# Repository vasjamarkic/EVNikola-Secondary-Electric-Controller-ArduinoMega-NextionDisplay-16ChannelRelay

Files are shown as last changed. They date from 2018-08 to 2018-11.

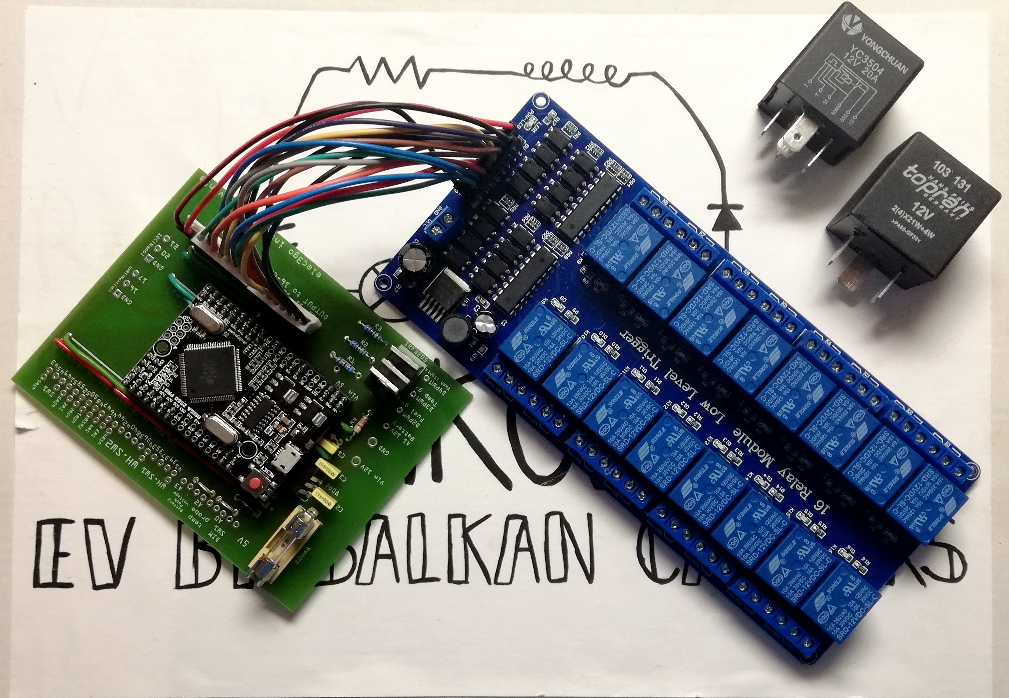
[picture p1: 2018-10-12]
mega2560_sheild and relay module connected.jpg

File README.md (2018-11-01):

# EVNikola-Secondary-Electric-Controller-ArduinoMegaPRO-NextionDisplay-i2cNano-16ChannelRelay
With Arduino Mega Robodyn Mini and Nextion touch display creating controller for lights and other actuators in VW T3.

Still to do:
- 
- recheck the code for wipers
- 
- place the battery and fusses under the co-driver's seat //insulate with plastic or plexi 
- wire the switches and microswitches in Nicola (test again the functions - wipers!!!)
- dismount the top dashboard
- get the front wipers and test it
- install the pwm module for the heating sistem. 
- clean and test the fan - putting the electric heater ??? use a fuse for that ...
- buy a heater (120 V DC) ??? Amazoon for 30 $ ....
- install the remaining front lights
- wire the key ignition switch with f16 and to Emsiso.
- solid the N.C. micro switch for handbrake
- solder the white LED and resistors, make connection types and place it in the dash, via PWM output. 

What was done:
- ordered the PCB board in Svet-elektronike (44 €), aquired.
- mount and assemble the pcb mega sheild (solder holders, mosfet, bridges, resistors, condensators, diodes, tube fuse ...)
- installed the rear LED lights (the small for targa not yet) (90 €)
- bought misc. material in EVJ (240 + 45 €)
- bought 4 relays (35 €), also from ebay for wipers
- wired the back lights and placed terminal under driver seat
- placed wires from fuses compartment (passenger seat) to central circuit compartments (driver seat)
- unmount fuel tank
- bought hexagonal spacers M3 >22 mm lenght (metal or nylon) - done, but will use 16-channel relay module!!! 
- mapping of all wires, matching with entities, dashboard, instrument board, ...
- Put in order de Relays with his functions.
- Choosed the fuses # for actuators 
- updated the drawing VISIO
- emergency stop lights with activating both turning lights - SOLVED with array and switch-case
- replaced the mega2560 with the new one because I accidently bricked 12V to the input pin --> UART is damaged, the procesor is not   
  communicating with pC anymore!
- wired the front-mask! 
- defined the 2d pack of fuses for PWM, Radio, cabin lights, other, Emsiso controller
- wired the wires and second fuse unit (f11 ÷ f16)
- placed wires from second pack fuses (f11 ÷ f16) to dashboard
- blinknig relay working
- placed the circuit box under the driver's seat
- wired the key ignition switch with fuse f10 to MCU.
- placed the wires for all dashboard switches (blue and white thin wires)

by Vasja Markič,
CEO at Elec3go Institute, SI

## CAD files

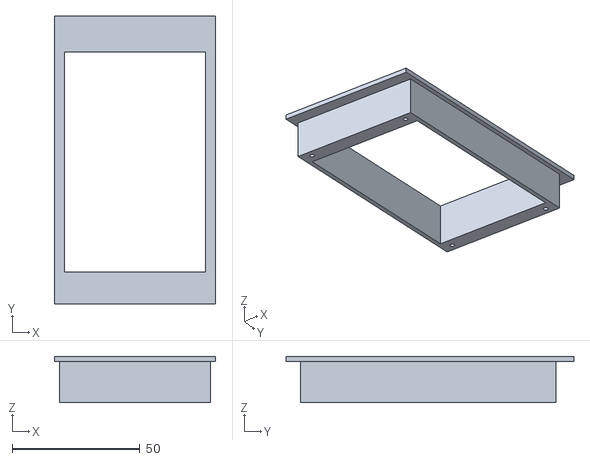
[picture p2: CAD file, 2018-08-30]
nextion2-vlozek.stl
63.0 x 112.5 x 18.0

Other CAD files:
nextion.skp

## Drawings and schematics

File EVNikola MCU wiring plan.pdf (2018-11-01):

# Top view GND

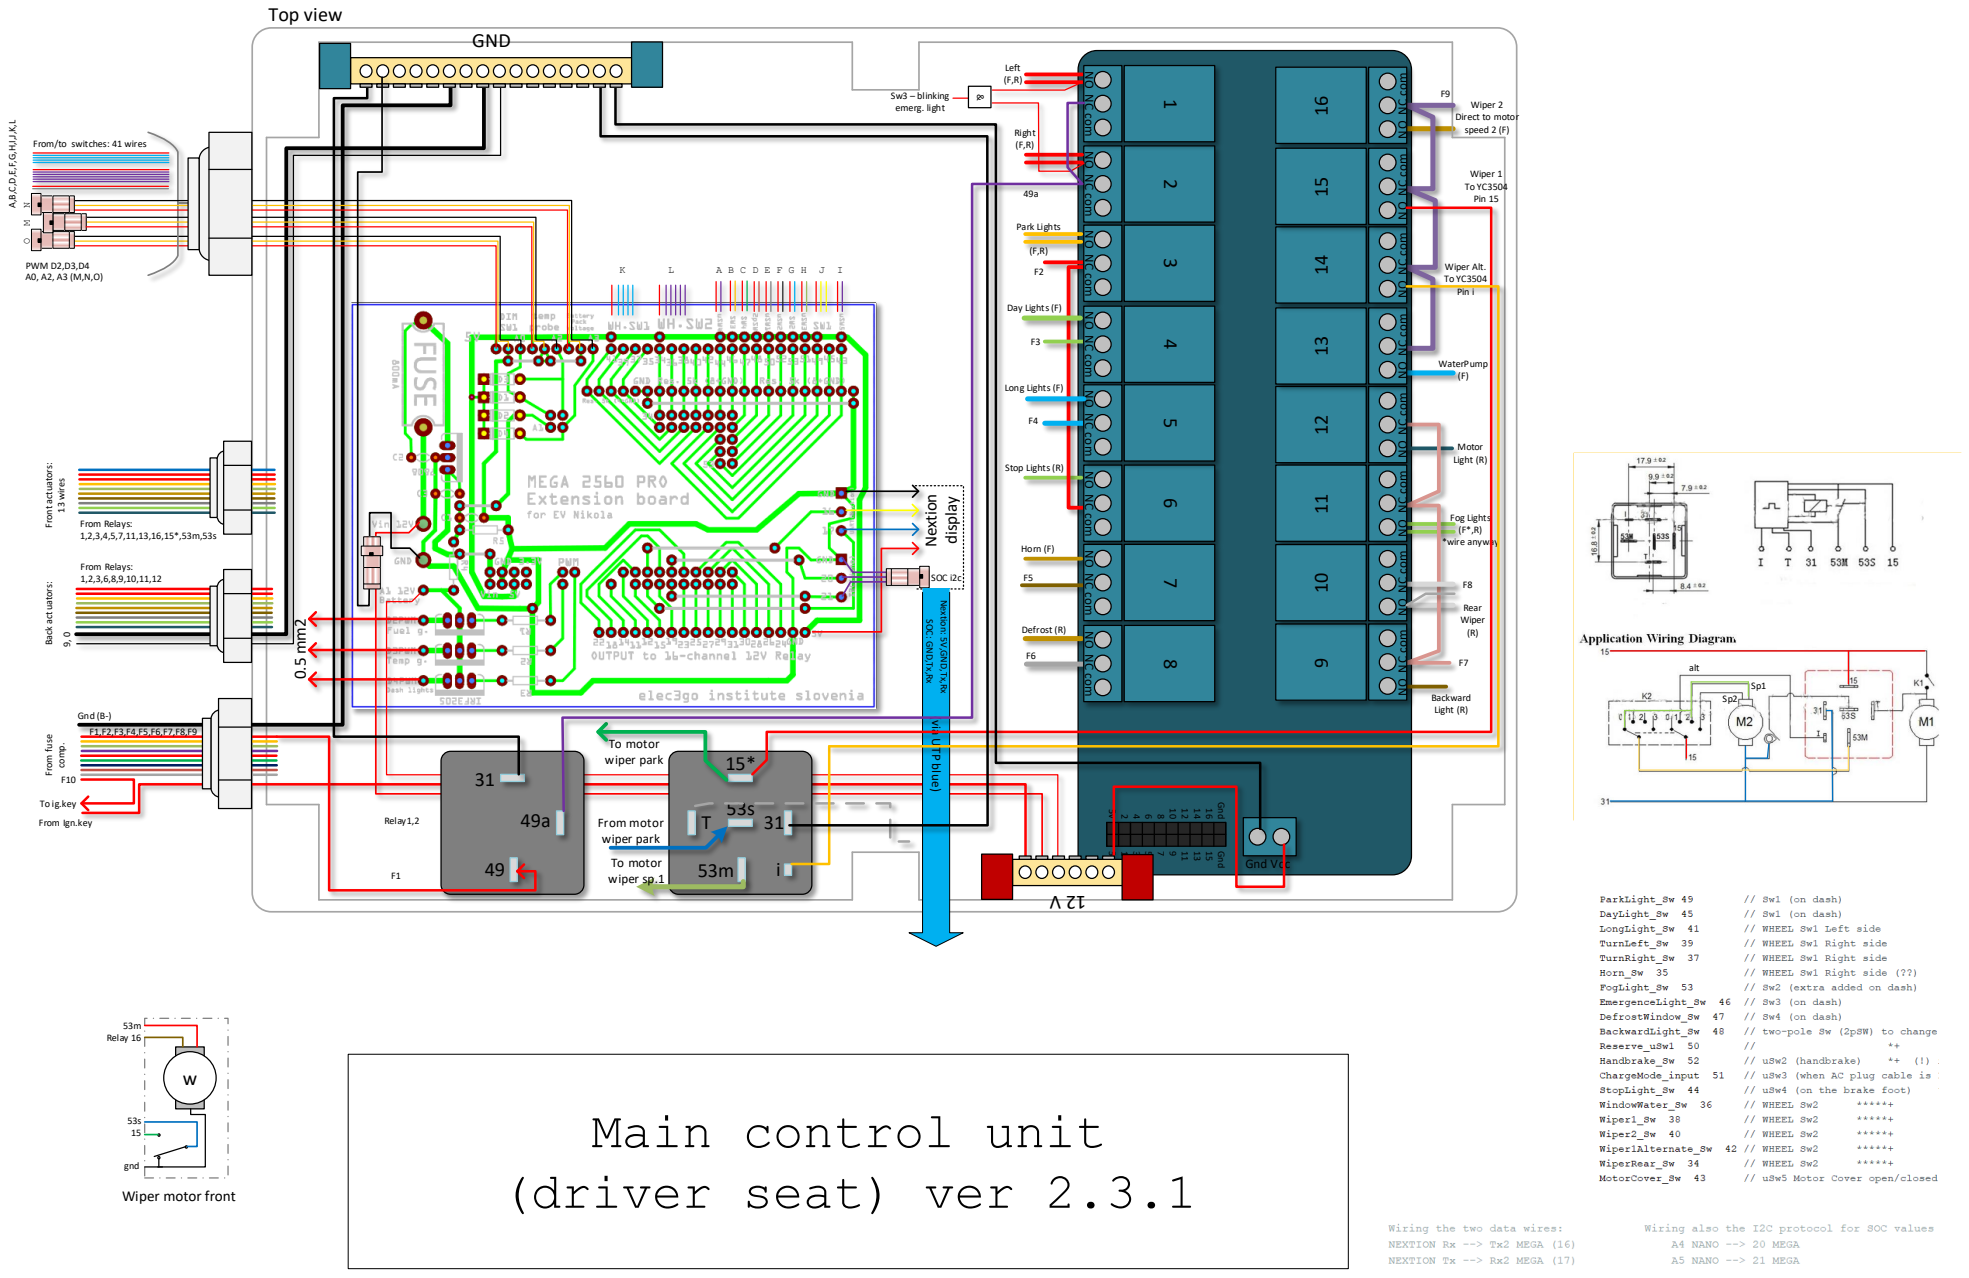
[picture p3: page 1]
Left (F,R); Right (F,R); Park Lights (F,R); Day Lights; Long Lights; Stop Lights; Horn; Defrost; Backward Light; Rear Wiper (R); Fog Lights (F*,R); *wire anyway; Motor Light; WaterPump (F); Wiper; 2 Direct to motor speed 2; alt; – blinking emerg. light; Gnd Vcc; Gnd; From Ign; .key; m Relay 16; Back actuators:; From Relays: 1,2,3,6,8,9,10; Front actuators:; 13 wires; From Relays: 1,2,3,4,5,7,11; PWM D; Nextion; display; SOC i; From; To motor wiper park; From motor wiper park; To motor wiper sp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

NO NC com

/to switches: 41 wires

Nextion: 5V,GND,Tx,Rx

SOC: GND,Tx,Rx

(via UTP blue)

Main control unit
(driver seat) ver

gnd
Wiper motor front

# Rear roof:

3

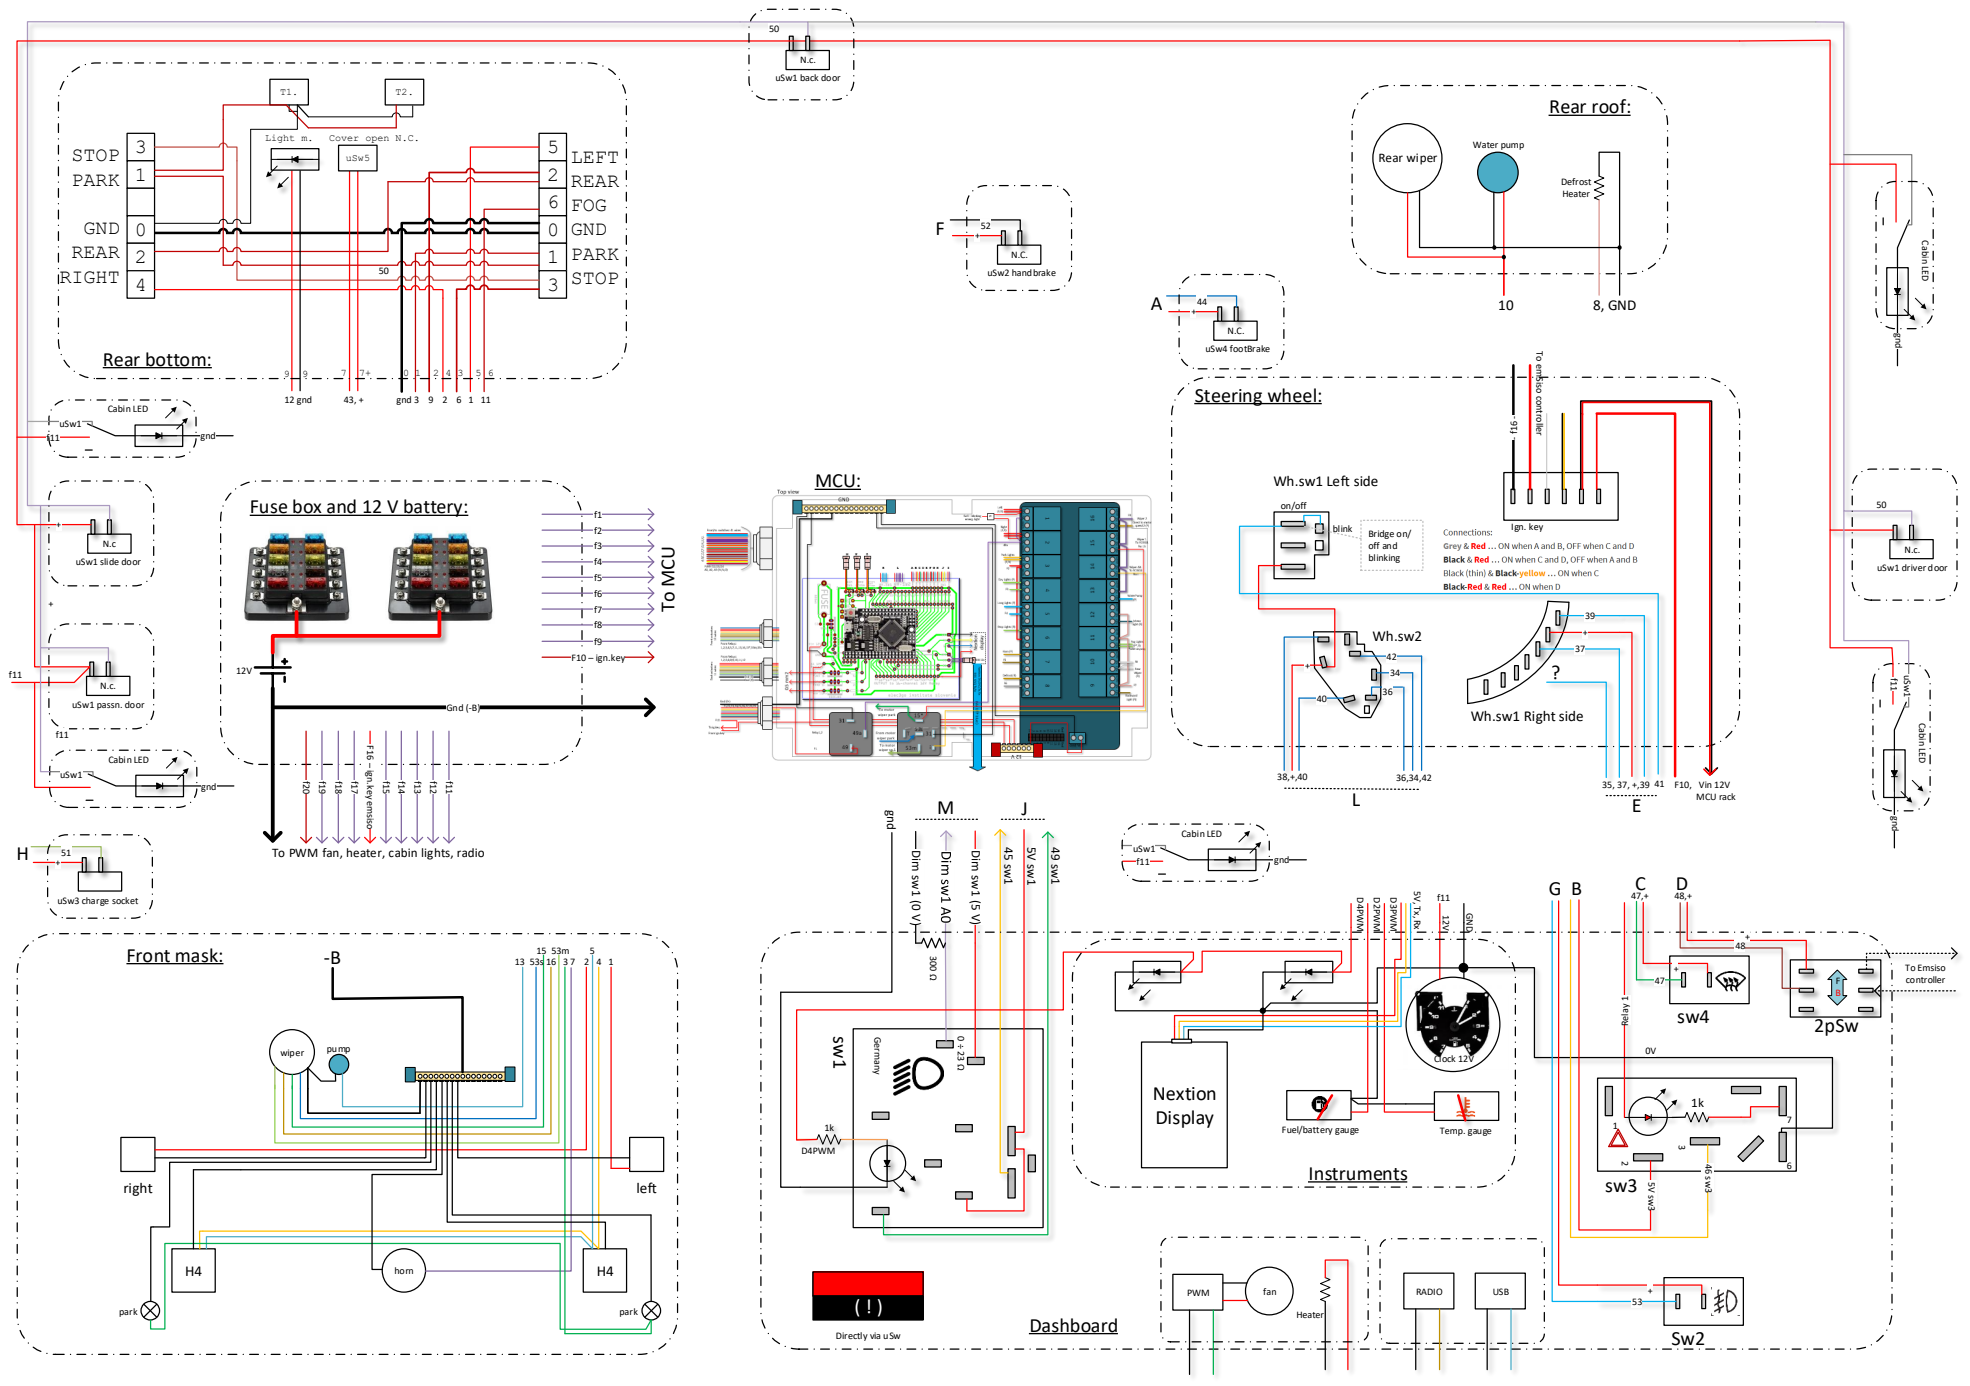
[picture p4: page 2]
Steering wheel:; 2pSw; Ign. key; Germany; Dim sw1 (0 V); Dim sw1 (5 V); D4PWM; To Emsiso controller; uSw1 driver door; uSw1 passn. door; uSw1 slide door; uSw1 back door; uSw2 handbrake; uSw3 charge socket; uSw4 footBrake; STOP; PARK; GND; REAR; RIGHT; LEFT; FOG; Rear bottom:; Cover open N.C.; uSw5; Light m.; 12 gnd; gnd 3 9 2 6 1 11; Front mask:; right; left; horn; park; wiper; pump; Dashboard; Fuel/battery gauge; Temp. gauge; D3PWM; D2PWM; Nextion Display; Instruments; Clock 12V; Relay 1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

To emSiso controller

Wh.sw1 Left side

Fuse box and 12 V battery:

Wh.sw1 Right side

F16 – ign.key emsiso

To PWM fan, heater, cabin lights, radio

Directly via uSw

F1
F2

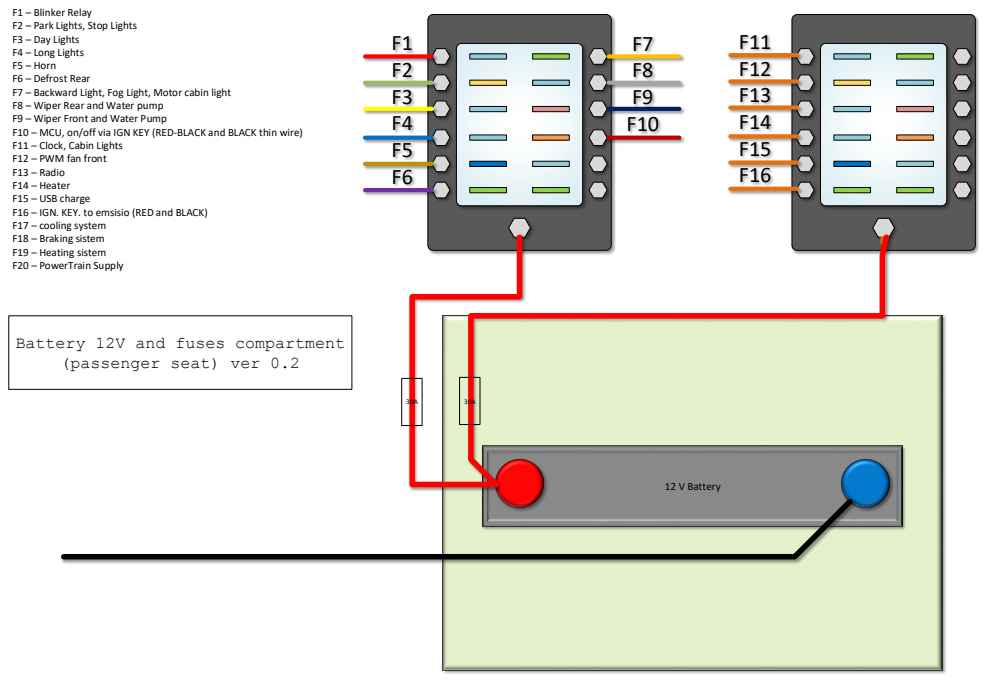
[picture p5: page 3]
12 V Battery

F1 – Blinker Relay
F2 – Park Lights, Stop Lights
F3 – Day Lights
F4 – Long Lights
F5 – Horn
F6 – Defrost Rear
F7 – Backward Light, Fog Light, Motor cabin light
F8 – Wiper Rear and Water pump
F9 – Wiper Front and Water Pump
F10 – MCU, on/off via IGN KEY (RED-BLACK and BLACK thin wire)
F11 – Clock, Cabin Lights
F12 – PWM fan front
F13 – Radio
F14 – Heater
F15 – USB charge
F16 – IGN. KEY. to emsisio (RED and BLACK)
F17 – cooling system
F18 – Braking sistem
F19 – Heating sistem
F20 – PowerTrain Supply

Battery 12V and fuses compartment

(passenger seat) ver 0.2

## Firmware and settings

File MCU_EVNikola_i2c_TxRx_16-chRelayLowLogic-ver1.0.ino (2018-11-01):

/*FIRST version NEXTION display with ARDUINO mega2560 PRO, connection working 
linked with HMI file "NEXTION_Nikola.hmi"
in "nexConf.h" enable debug and must be set to Serial2 ...
Wiring the two data wires:            Wiring also the I2C protocol for SOC values from arduino NANO
NEXTION Rx --> Tx2 MEGA (16)              A4 NANO --> 20 MEGA
NEXTION Tx --> Rx2 MEGA (17)              A5 NANO --> 21 MEGA
The input signals are Swing icons on display - I used ProgressBAR for that trick!
Make sure you import the ITEADlib library in arduino IDE!!
The Relay module has to be connected to power a 10 seconds after the key power the Arduino & Nextion to prevent Swing relays ON!
Dimming the display with tuch function (Nextion code)
Dimming the dash lights with potentimeter on dashboard Sw1
11.9. 2018 fix the code (I/O pins) for MEga PRO CH340G. PINS from 2 ÷ 13 are PWM. 
13.9.2018 Upddated the pin numbers for the Shield (fritzing PCB sheme), emergency lights will turn with both Relay 4 and 5 
via 103 131 topran 12V flashing relay: pins - 49 (+12V), 49a (LOAD), 31 (GND)
Added MotorCover microSw Input and Motor compartment light (Output)
Relay 12 turns the motorlights.
30.9.2018 Updated the Output pins with shematic "EVnikola Omarca Robodyn krmilje postavitev" (VISIO)
24.10. Solved the sloow switching - using an Array for storing input states, then aktivating the logic only when the change is commited, 
Using indexing and switch-case! Also the emergency outputs works fine now!!!
26.10. eliminated all small errata in I/O displaying Nextion, added a graphic shiny LED!

Author: Vasja Markič           
*/
#include <Wire.h>
#include <doxygen.h>
//#include <NexButton.h>
#include <NexConfig.h>
//#include <NexCrop.h> //#include <NexGauge.h> //#include <NexHardware.h> //#include <NexHotspot.h> //#include <NexObject.h> //#include <NexPage.h>
#include <NexPicture.h>
#include <NexProgressBar.h>
//#include <NexSlider.h> //#include <NexText.h>
#include <Nextion.h>
#include <NexTouch.h>
//#include <NexWaveform.h>
#include "Nextion.h"

// OUTPUTS pin declaration:
#define TurnLeft 22              // relay 1 - 2x left turning lights (via flashing relay 103 131)
#define TurnRight 25             // relay 2 - 2x right turning lights (via flashing relay 103 131) (both - emergency stop - turns on via Sw3)
#define ParkLight 18             // relay 3 - 2x front parklights, 2x back parklights + registratiton tables lights, PWM dashboard ON
#define DayLight  27             // relay 4 - 2x front daylights H4
#define LongLight  14            // relay 5 - 2x front longlights H4
#define StopLight  29            // relay 6 - 2x back stoplights
#define Horn  11                 // relay 7 - to horn acuator
#define DefrostWindow  31        // relay 8 - to rear window defrost
#define BackwardLight  12        // relay 9 - to rear backlight(s)
#define WiperRear  30            // relay 10 - motorpump rear AND motor wiper rear
#define FogLight  15             // relay 11 - 2x front foglights
#define MotorLight  28           // relay 12 - lights when cover motor is up ...
#define WindowWater  19          // relay 13 - motorpump front
#define Wiper1Alternate  26      // relay 14 - via auto wiper intermittent relay to motor wiper front, timer
#define Wiper1  23               // relay 15 - wire to auto wiper intermittent relay
#define Wiper2  24               // relay 16 - wire directly to wiper motor
// 21, 20 reserved for I2C comm with NANO soc-meter
// 17, 16 reserved for Tx2 and Rx2 comm with Nextion display
// 13 reserved integrated LED       // n.c.

// PWM OUTUPTS (from 0 ÷ 13)
#define DashLightPWM  4   // dimm dashboard lights
#define TempGaugePWM  3    // drive temp. gauge
#define FuelGaugePWM  2    // drive voltage pack (ex. fuel) gauge

// INPUTS:
#define ParkLight_Sw 49        // Sw1 (on dash)                 **+ --> 3x singal wires, 1x GND and 1x 5V supply
#define DayLight_Sw  45        // Sw1 (on dash)                 **+
#define LongLight_Sw  41       // WHEEL Sw1 Left side           ****+  --> 4x signal wires and 1x 5V supply
#define TurnLeft_Sw  39        // WHEEL Sw1 Right side          ****+
#define TurnRight_Sw  37       // WHEEL Sw1 Right side          ****+
#define Horn_Sw  35            // WHEEL Sw1 Right side (??)     ****+
#define FogLight_Sw  53        // Sw2 (extra added on dash)        *+
#define EmergenceLight_Sw  46  // Sw3 (on dash)                    *+
#define DefrostWindow_Sw  47   // Sw4 (on dash)                    *+
#define BackwardLight_Sw  48   // two-pole Sw (2pSW) to change the drive direction! (on dash, added extra!)   *+
#define Reserve_uSw1  50       //                     *+  
#define Handbrake_Sw  52       // uSw2 (handbrake)    *+  (!) icon on NEXTION
#define ChargeMode_input  51   // uSw3 (when AC plug cable is IN, rezervoir tank)   *+
#define StopLight_Sw  44       // uSw4 (on the brake foot)    *+
#define WindowWater_Sw  36     // WHEEL Sw2      *****+
#define Wiper1_Sw  38          // WHEEL Sw2      *****+
#define Wiper2_Sw  40          // WHEEL Sw2      *****+
#define Wiper1Alternate_Sw  42 // WHEEL Sw2      *****+
#define WiperRear_Sw  34       // WHEEL Sw2      *****+
#define MotorCover_Sw  43      // uSw5 Motor Cover open/closed *+

// analoge INPUTS (from A0 ÷ A15)
#define DIM_input  A0                 // potentiometer on Sw1, for dimming the dash Lights    ***-+
#define Battery12V_input  A1          // analog input, resistor divider 1:15 ratio with capacitor   *-+
#define BatteryPackVolt_input  A3     // analog input, 86V ÷ 125V range via resistor divider R1 = 12K, R2 = 500E --> input range 3.44V ÷ 5V   ???? (GND NOT common!)
#define Temperature_input  A2         // depends on the PTK probe!   ???

// ventilation via PWM power module
// heating via high voltage heater???
// display SOC - using existing fuel gauge (0 ÷ 6 V) reading analog IN and drive with digital PWM and MOSFET BS 170 ali BS 107.
// display temp. motor (0 ÷ 6 V)

// variables will change - HIGH state relay OFF:
int ParkLight_Sw_ON = true;
int DayLight_Sw_ON = true;
int LongLight_Sw_ON = true;
int TurnLeft_Sw_ON = true;
int TurnRight_Sw_ON = true;
int EmergenceLight_Sw_ON = true;
int StopLight_Sw_ON = true;
int Horn_Sw_ON = true;
int DefrostWindow_Sw_ON = true;
int BackwardLight_Sw_ON = true;
int CabinLight_Sw_ON = true;
int Reserve_uSw1_ON = true;
int MotorCover_Sw_ON = true;
int Handbrake_Sw_ON = true;
int WiperRear_Sw_ON = true;
int WindowWater_Button_ON = true;
int Wiper1Alternate_Sw_ON = true;
int Wiper1_Sw_ON = true;
int Wiper2_Sw_ON = true;
int FogLight_Sw_ON = true;
int ChargeMode_ON = true;       // if we plug the AC charging
long DIM_Value = 0;      // initial value of the dimming display, from 0 to 1023  (measures 0 ÷ 5 V)
long DIM;                        // DIM transformed to int from 0 ... 100
unsigned int Battery12V_Value = 0;    // initial value od digital value of the 12 V battery (0 ÷ 1023) 
unsigned int BatteryPackVolt_Value = 0;
unsigned int Temperature_Value = 0;
unsigned int Battery12V_treshold = 11;   // set the min. voltage for signaling battery low voltage on display
float Battery12V;
long BatteryPackVolt;      // transform 3.44V to 0 and 5.00V to 40
long Temperature;         // transform 0.00V to 0 and 5.00V to 40
char object[10];
int SOC2;         //aquire from arduino NANO SOC Meter
volatile double ARRAY[20];          // for storing input from switches
volatile double ARRAY_OLD[20];      // the loop before, for trigering an event!

// Declaration of objects in NEXTION
// NexProgressBar - progress bar --> value 100 (is pic1) or 0 (pic0)
// NexButton ...
NexProgressBar j0 = NexProgressBar(0, 3, "j0");   // day lights
NexProgressBar j1 = NexProgressBar(0, 4, "j1");   // long lights
NexProgressBar j2 = NexProgressBar(0, 5, "j2");   //  fog
NexProgressBar j3 = NexProgressBar(0, 6, "j3");   //  left
NexProgressBar j4 = NexProgressBar(0, 7, "j4");   //  right
NexProgressBar j5 = NexProgressBar(0, 8, "j5");   //  EmergenceLight
NexProgressBar j6 = NexProgressBar(0, 9, "j6");   //  handbrake
NexProgressBar j7 = NexProgressBar(0, 10, "j7");   //  batery low
NexProgressBar j8 = NexProgressBar(0, 11, "j8");   //  defrozing window
NexProgressBar j9 = NexProgressBar(0, 12, "j9");      // AC recharge lightning
NexProgressBar j10 = NexProgressBar(0, 13, "j10");    // "Nicola" text diplay or "Charging" text display
NexProgressBar j11 = NexProgressBar(0, 14, "j11");    // Displaying the progress bar value of SOC, "0" empty, "100" full.
// write here for displaying SOC value ...
NexProgressBar j12 = NexProgressBar(0, 15, "j12");    // icon charging inside the van
NexProgressBar j13 = NexProgressBar(0, 16, "j13");    // slider of Dimming brightness of dashboard lights
NexProgressBar j14 = NexProgressBar(0, 19, "j14");    // Cover motor open!
NexProgressBar j15 = NexProgressBar(0, 17, "j15");    // Backward icon on display
NexProgressBar j16 = NexProgressBar(0, 20, "j16");    // PARK light

// Declaration of touch events: (temp. the list is empty)
NexTouch *nex_listen_list[] =
{
  NULL
};

//Touch events:
// if needed write down here 

//*******************************************************************************************************
// setup program/sequence:
void setup() {
  nexInit();               // Nextion initalization
  Wire.begin(8);   // I2C !!
  Wire.onReceive(receiveEvent);
  Serial.begin(9600);      // speed of comunication with Arduino

//register the event callback functions of each event
// OUTPUTS:
  pinMode(TurnLeft, OUTPUT);           // relay 1
  pinMode(TurnRight, OUTPUT);          // relay 2
  pinMode(ParkLight, OUTPUT);          // relay 3
  pinMode(DayLight, OUTPUT);           // relay 4
  pinMode(LongLight, OUTPUT);          // relay 5
  pinMode(StopLight, OUTPUT);          // relay 6
  pinMode(Horn, OUTPUT);               // relay 7: 1 x Horn
  pinMode(DefrostWindow, OUTPUT);      // relay 8
  pinMode(BackwardLight, OUTPUT);      // relay 9
  pinMode(WiperRear, OUTPUT);          // relay 10: back wiper and watering
  pinMode(FogLight, OUTPUT);            // relay 11
  pinMode(MotorLight, OUTPUT);          // relay 12 Lights in motor compartment
  pinMode(WindowWater, OUTPUT);         // relay 13 motor of water pump front
  pinMode(Wiper1Alternate, OUTPUT);     // relay 14
  pinMode(Wiper1, OUTPUT);              // relay 15
  pinMode(Wiper2, OUTPUT);              // relay 16 
  pinMode(DashLightPWM, OUTPUT);        // to MOSFET 1  drives dash lights via RELAY 1 (5 V), mosfet driven with 12 V
  pinMode(TempGaugePWM, OUTPUT);        // to MOSFET 2  drives tempertature GAUGE (6 V), mosfet driven on 12 V
  pinMode(FuelGaugePWM, OUTPUT);        // to MOSFET 3 drives fuel GAUGE (6 V), mosfet driven on 12 V
  
// INPUTS:
  pinMode(ParkLight_Sw, INPUT);
  pinMode(DayLight_Sw, INPUT);
  pinMode(LongLight_Sw, INPUT);       
  pinMode(TurnLeft_Sw, INPUT);   
  pinMode(TurnRight_Sw, INPUT);  
  pinMode(StopLight_Sw, INPUT);    // foot pedal microbutton
  pinMode(Horn_Sw, INPUT);         // steering wheel button
  pinMode(DefrostWindow_Sw, INPUT); 
  pinMode(BackwardLight_Sw, INPUT);     // Two-poles Sw 
  pinMode(WiperRear_Sw, INPUT);  
  pinMode(EmergenceLight_Sw, INPUT);   
  pinMode(Reserve_uSw1, INPUT); 
  pinMode(MotorCover_Sw, INPUT);
  pinMode(Handbrake_Sw, INPUT);
  pinMode(FogLight_Sw, INPUT);
  pinMode(WindowWater_Sw, INPUT);       
  pinMode(Wiper1Alternate_Sw, INPUT);  
  pinMode(Wiper1_Sw, INPUT);  // speed 1
  pinMode(Wiper2_Sw, INPUT);  // speed 2 
  pinMode(ChargeMode_input, INPUT); // if the AC cable is pludged
  pinMode(Battery12V_input, INPUT); // ANALOG measurment of voltage 0 ÷ 12 V - wire a voltage divider with resistors 81.3k + (8.25k || 100nF)
  pinMode(DIM_input, INPUT);    // dimming with trimmer on Sw1 (lights), 0 - 5V (1023), could also trim the LCD brightness (ANALOG)
  pinMode(BatteryPackVolt_input, INPUT);   // range from 3.44V (703) to 5V (1023)   (ANALOG)  // GNDs must be separated!!!
  pinMode(Temperature_input, INPUT);    // from 0V (0) to 5V (1023) via PTK   (ANALOG)
  
  relayOFF();       //sets all relay to OFF!
  testDisplay();     // test all the icons for 0.5 sec
}
//***************************************************************************************************
//main loop/program :
void loop() {  
  readDigital();      // reading the input states into an ARRAY
  readAnalog();       // reading the input ANALOG 
  equations();
  writeDigital();    //Solved with software interrupt - if change in switches! Used Switch-Case
  writeAnalog();    
  nexLoop(nex_listen_list);    // reading the touch events on NEXTION display (curently not used)
}
//*********************************************************************************************
//function for reading digital and analog signals in Arduino:
void readDigital() {

// read the state of the inputs and store it in a Array size 20

  for (int i = 0; i < 20; i++) {
  ARRAY_OLD[i]=ARRAY[i];        // store the last data to the ARRAY_OLD.
  }
  ARRAY[0] = digitalRead(TurnLeft_Sw);     //New readings and storing in ARRAY
  ARRAY[1] = digitalRead(TurnRight_Sw);
  ARRAY[2] = digitalRead(ParkLight_Sw);
  ARRAY[3] = digitalRead(DayLight_Sw);
  ARRAY[4] = digitalRead(LongLight_Sw);
  ARRAY[5] = digitalRead(StopLight_Sw);
  ARRAY[6] = digitalRead(EmergenceLight_Sw); 
  ARRAY[7] = digitalRead(ChargeMode_input);
  ARRAY[8] = digitalRead(Horn_Sw);
  ARRAY[9] = digitalRead(DefrostWindow_Sw);
  ARRAY[10] = digitalRead(BackwardLight_Sw);
  ARRAY[11] = digitalRead(WiperRear_Sw);
  ARRAY[12] = digitalRead(Reserve_uSw1);
  ARRAY[13] = digitalRead(MotorCover_Sw);
  ARRAY[14] = digitalRead(Handbrake_Sw);
  ARRAY[15] = digitalRead(FogLight_Sw);
  ARRAY[16] = digitalRead(WindowWater_Sw);
  ARRAY[17] = digitalRead(Wiper1Alternate_Sw);
  ARRAY[18] = digitalRead(Wiper1_Sw);
  ARRAY[19] = digitalRead(Wiper2_Sw);
}
 
//******************************************************************************************
void writeDigital() {
  if (ARRAY != ARRAY_OLD) {              // if any switch activated, one of the digit is different, compare the OLD and NEW ARRAY
    for (int i = 0; i < 20; i++) {       // check all inputs in the array
    if (ARRAY_OLD[i]!=ARRAY[i]){          // when found the index (changed input), change the status!
      switch (i) {
        case 0:                         // turn left
        j3.setValue(ARRAY[i]*100);
        digitalWrite(TurnLeft, !ARRAY[i]);
        break;
        case 1:                       // turn right
        j4.setValue(ARRAY[i]*100);
        digitalWrite(TurnRight, !ARRAY[i]);
        break;
        case 2:                           // park light
        digitalWrite(ParkLight, !ARRAY[i]);
        j16.setValue(ARRAY[i]*100);
        // set PWM D4 LED cockpit ON DIM Value in the function writeAnalog()
        //analogWrite(DashLightPWM,!ARRAY[i]*DIM); --> into the writeAnalog() function
        break;
        case 3:                         // day lights
        j0.setValue(ARRAY[i]*100);
        digitalWrite(DayLight, !ARRAY[i]);
        break;
        case 4:                         // long lights
        j1.setValue(ARRAY[i]*100);
        digitalWrite(LongLight, !ARRAY[i]);
        break;
        case 5:                         // stop light
        digitalWrite(StopLight, !ARRAY[i]);
        break;
        case 6:                         // Emergence blinkers
        digitalWrite(TurnRight, !ARRAY[i]);
        digitalWrite(TurnLeft, !ARRAY[i]);
        j5.setValue(ARRAY[i]*100);
        break;
        case 7:                          // CHARGE mode input
        j9.setValue(ARRAY[i]*100);   //Strela
        j10.setValue(!ARRAY[i]*100);   // Show "charging" 
        j12.setValue(ARRAY[i]*100);    // icon charging
        break;
        case 8:                       // HORN
        digitalWrite(Horn, !ARRAY[i]);
        break;
        case 9:                        // DEFROST
        j8.setValue(ARRAY[i]*100);
        digitalWrite(DefrostWindow, !ARRAY[i]);
        break;
        case 10:                   // BackWard Light
        j15.setValue(ARRAY[i]*100);         // icon going back!!!
        digitalWrite(BackwardLight, !ARRAY[i]);
        break;
        case 11:                          // Wiper REAR + WATER
        digitalWrite(WiperRear, !ARRAY[i]);
        break;
        case 12:                          // RESERVE uSw1
        break;
        case 13:                          // Motor cover - light back motor compartment
        j14.setValue(ARRAY[i]*100);
        digitalWrite(MotorLight, !ARRAY[i]);
        break;
        case 14:                        // Handbrake
        j6.setValue(ARRAY[i]*100);
        break;
        case 15:                        // Fog Light
        j2.setValue(ARRAY[i]*100);
        digitalWrite(FogLight, !ARRAY[i]);
        break;
        case 16:                        // Window WATER front
        digitalWrite(WindowWater, !ARRAY[i]);
        break;
        case 17:                        // Wiper 1 ALT
        digitalWrite(Wiper1Alternate, !ARRAY[i]);
        break;
        case 18:                        // WIPER 1
        digitalWrite(Wiper1, !ARRAY[i]);
        break;
        case 19:                        // WIPER 2
        digitalWrite(Wiper2, !ARRAY[i]);
        break;       
        }
      }
    }
  }
// dim the display - reading DIM_value, using potenciometer on A0
// On nextion HMI file the page0 postinitialize event has code: j13.value=dim
  j13.setValue(DIM);    //displaying the brigtness of the dash lights. 
// Displaying SOC graphic via wire.h on NANO 
  j11.setValue(SOC2);    // when aquiring data from Arduino NANO, change to SOC2! 
//  Serial.println(SOC2);         // for diagnostic!

/* display of low 12v battery icon, if voltage is lower than 11 V reading from A11
  0 - ~17 V voltmeter
  works with 3.3volt and 5volt Arduinos
  uses the stable internal 1.1volt reference
  10k resistor from A0 to ground, and 150k resistor from A0 to +batt
  (1k8:27k or 2k2:33k are also valid 1:15 ratios)
  100n capacitor from A0 to ground for stable readings    */
  Battery12V=Battery12V_Value/19.5533;  // calculation to voltage value
  //Serial.println(Battery12V_Value);   // for monitoring purpouses
  //Serial.println(Battery12V);
  if (Battery12V < Battery12V_treshold) {      //set the voltage treshold
    j7.setValue(100);
    }
  else {
    j7.setValue(0);
    }
}

void writeAnalog() {
  analogWrite(FuelGaugePWM, BatteryPackVolt);   // wire to gauge fuel
  analogWrite(TempGaugePWM, Temperature);       // wire to Temp. gauge. 
  analogWrite(DashLightPWM, ARRAY[2]*DIM);      //the third field in the array is ParkLight input switch.
  }
  
void readAnalog() {
  DIM_Value = analogRead(DIM_input); // reading values from 0 - 5 V and converts to int value from 0 to 1023 .
  Battery12V_Value = analogRead(Battery12V_input);
  BatteryPackVolt_Value = analogRead(BatteryPackVolt_input);
  Temperature_Value = analogRead(Temperature_input);
  }

void equations() {
  //equations for DIMMING LED cockpit lights:
  // 950 --> 100, 1023 --> 255; ???? resistor divider - 300 Ohm and 23 Ohm pot. , 5V --> Max 5 V (1023), Min 4.64 V (950)
  DIM=3.49*(1023-DIM_Value);   //min 0 max 73 --> multiply faktor 3.49 --> min 0 max 255
  //equations for Fuel gauge:
  // 703 --> 0, 1023 --> 255    BUT - GND of the pack is insulated from the circuits!!!
  BatteryPackVolt = (BatteryPackVolt_Value-703)*255/(1023-703);
  //equations for Temperature gauge:
  // 0 --> 0, 1023 --> 255
  Temperature = Temperature_Value*255/1023;
  // sending PWM singal temperature gauge and fuel gauge:
}

//function for reading via I2C the SOC from Nano
void receiveEvent(int howMany) {
  while (1 < Wire.available()) { // loop through all but the last
    char c = Wire.read(); // receive byte as a character
    //Serial.print(c);         // print the character
  }
  SOC2 = Wire.read();    // receive byte as an integer
  //Serial.println(SOC2);         // print the integer
}

// set all relay OFF - for begin sequence!
void relayOFF() {
  digitalWrite(TurnLeft, HIGH);
  digitalWrite(TurnRight, HIGH);
  digitalWrite(ParkLight, HIGH);
  digitalWrite(DayLight, HIGH);
  digitalWrite(LongLight, HIGH);
  digitalWrite(StopLight, HIGH);
  digitalWrite(Horn, HIGH);
  digitalWrite(DefrostWindow, HIGH);
  digitalWrite(BackwardLight, HIGH);
  digitalWrite(WiperRear, HIGH);
  digitalWrite(FogLight, HIGH);
  digitalWrite(MotorLight, HIGH);
  digitalWrite(WindowWater, HIGH);
  digitalWrite(Wiper1Alternate, HIGH);
  digitalWrite(Wiper1, HIGH);
  digitalWrite(Wiper2, HIGH);
  }

void testDisplay() {
  j0.setValue(100);
  j1.setValue(100);
  j2.setValue(100);
  j3.setValue(100);
  j4.setValue(100);
  j5.setValue(100);
  j6.setValue(100);
  j7.setValue(100);
  j8.setValue(100);
  j9.setValue(100);
  j10.setValue(0); 
  j11.setValue(100);
  j12.setValue(100);
  j13.setValue(100);
  j14.setValue(100);
  j15.setValue(100);
  j16.setValue(100);
  delay(500);
   j0.setValue(0);
  j1.setValue(0);
  j2.setValue(0);
  j3.setValue(0);
  j4.setValue(0);
  j5.setValue(0);
  j6.setValue(0);
  j7.setValue(0);
  j8.setValue(0);
  j9.setValue(0);
  j10.setValue(100); 
  j11.setValue(0);
  j12.setValue(0);
  j13.setValue(0);
  j14.setValue(0);
  j15.setValue(0);
  j16.setValue(0);
  }

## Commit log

2018-08-18 Code for Arduino Mega
    Using Arduino Mega in connection with Nextion display, 16-chanell low logic optocoupler relay module.
2018-08-18 Tutorial Nextion
    How to - use, program and connect to Arduino (Mega).
2018-08-29 icons and logo for Nextion display 2.4"
    Black background, icons and battery SOC meter, BalkanCampers logo.
2018-08-30 Holder for Nextion Display
    3D model (sketchup and STL) for Nextion holder for VW T3 instrumentation
    [nextion.skp, nextion2-vlozek.stl]
2018-09-11 Fix the code for the control unit usingROBOTDYN MEGA PRO CH340G /Atmega2560
    Added:
    - 3 PWM outputs for driving the dashboard lights, voltage and temperature gauges
    - 3 analog inputs for measuring dim, voltage of the battery pack (via resistor divider) and temperature.
    Changed:
    - cabin lights will be drived directly! (not via central unit)
    - added the rear wiper function
2018-09-11 PIN chart for Arduino MegaPro
2018-09-13 Version 1.1
    Changed the pin order, according with the PCB sheild drawn in fritzing for MegaPro unit
2018-09-13 Ver 0.1
    Added the holders for MegaPro, resistors, connectors digital I/O, UART and I2C.
    To add security circuit (DIODES), PWM with transistors, analog inputs with dividers and filters, power stabilizer 5 V.
    [ControlUnit Sheild for MegaPro RoboDyn EVNikolaProject PCB.fzz]
2018-09-13 MOSFET irf3205 datasheet
2018-09-13 Updated fritzing and c code for Arduino
    Ver. 1.2
    [ControlUnit Sheild for MegaPro RoboDyn EVNikolaProject PCB.fzz]
2018-09-16 Upper limit for PWM set to 255!
2018-09-17 Added 7805 voltage stabilizator and fuse.
    [ControlUnit Sheild for MegaPro RoboDyn EVNikolaProject PCB.fzz]
2018-09-17 Last version PCB
    [ControlUnit Sheild for MegaPro RoboDyn EVNikolaProject PCB.fzz]
2018-09-19 Added pin 5V to 16-chanel relay output
    [ControlUnit Sheild for MegaPro RoboDyn EVNikolaProject PCB.fzz]
2018-09-30 Updated pins
    Next step: Timer as interupt for blinking
2018-09-30 Wiring diagram for control unit
    The magic box will be placed under the drive's seat.
2018-10-12 last version
    [ControlUnit Sheild for MegaPro RoboDyn EVNikolaProject PCB.fzz]
2018-10-12 last update wiring
2018-10-12 Picture of microcontroler and shield + 16ch relay
2018-10-12 PCB drawings for production
    In Fritzing, all layers, Svet elektronike 2 pc for 45 €
2018-10-19 Almost finishing wiring ...
2018-10-20 Testing the code with hardware connected and relay
2018-10-21 PDF witing AtMEga2560 and actuators, Relay, fuses
2018-10-23 version 1.0 arduino mega 2560 working
    The lag is reduced to min thanks to ARRAY solution and switch-case structure.
    Updated for working with NEXTION 3.5"
2018-11-01 Ver. 1.0.2
    DIM working while park off - updated and solved the errata.
    [MCU_EVNikola_i2c_TxRx_16-chRelayLowLogic-ver1.0.ino]
